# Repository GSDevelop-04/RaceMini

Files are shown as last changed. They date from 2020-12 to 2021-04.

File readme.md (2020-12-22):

<br />
<p align="center">
   <a href="https://github.com/GSDevelop-04/RaceMini">
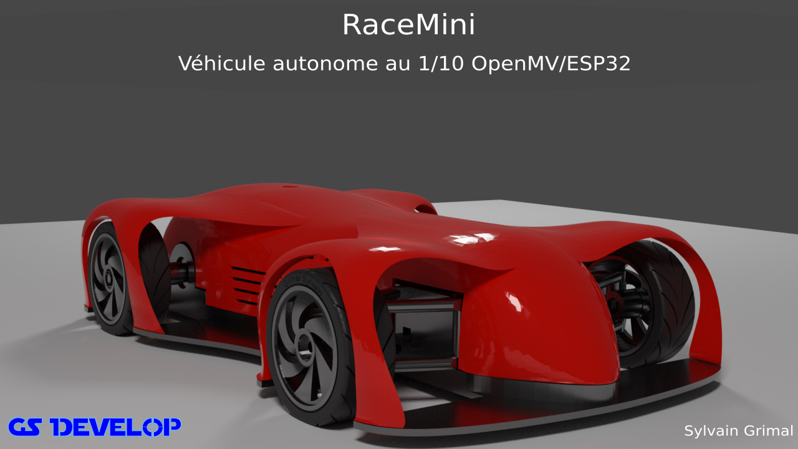
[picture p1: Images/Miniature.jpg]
    
   </a>
   <br/>
   Véhicule autonome au 1/10
   1/10 self driving car
</p>

##    1) Introduction

RaceMini est un véhicule au 1/10 d'étude sur la conduite autonome.
cliquer pour voir la vidéo sur youtube:
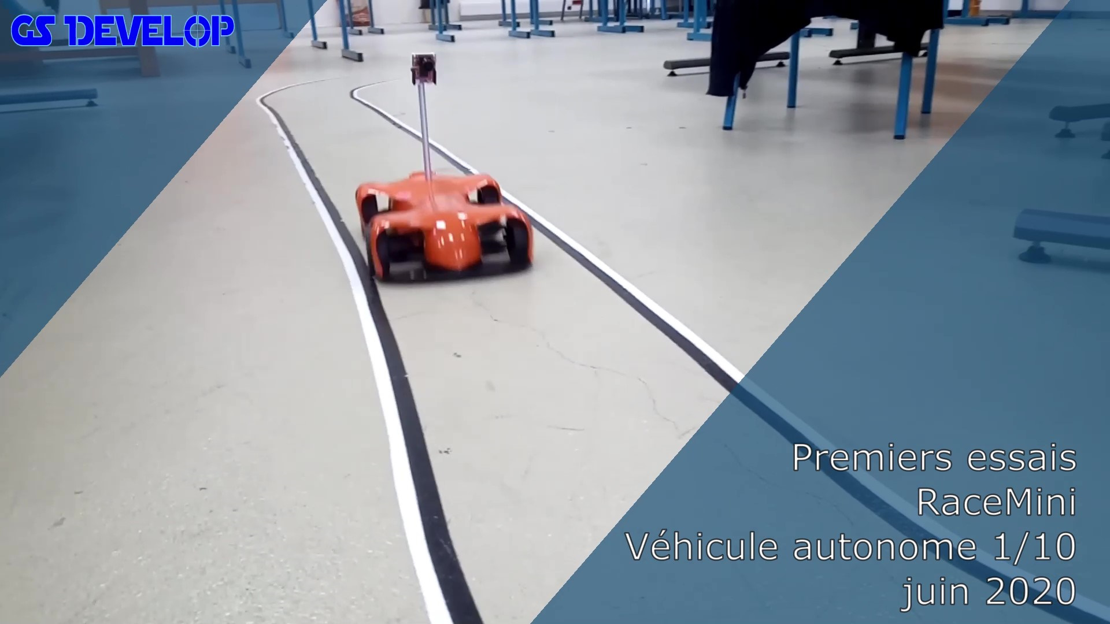
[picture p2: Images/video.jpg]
Vidéo (https://youtu.be/tJVRatMsotc)


Le véhicule peut être piloté par un smartphone via une application Android et peut fonctionner en automatique ou manuel. Il utilise la reconnaissance des marquages au sol via la transformée de Hough sur une caméra openMV M7 ou H7 

<p align="center">
 <a href="https://github.com/GSDevelop-04/RaceMini">
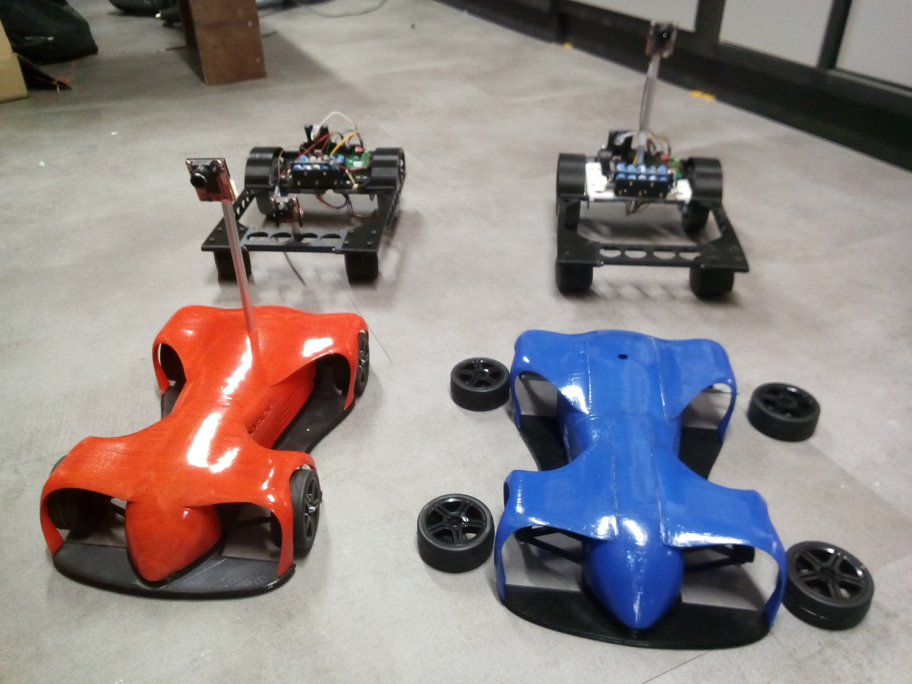
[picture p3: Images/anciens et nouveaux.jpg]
véhicules
    
 </a>
</p>

Le modèle est entierement imprimable en 3D

**Dans le dépot RaceMini vous trouverez :**

* les fichiers CAO, STL pour imprimantes 3D 20 x 20 cm ou 30 x 30 cm
* L'APK Android pour le téléphone
* Le source ESP32 pour IDE Arduino
* Le source Python pour L'OpenMV

Non obligatoire:
* Les fichiers kiCad pour la fabrication d'un circuit imprimé: il rationalise le câblage avec des connecteurs pour chaque élément du système ( carte variateur, alim 5V, camera, écran )
* Des examples de traitement de l'image (transformée de Hough et régréssion) en java script (juste pour comprendre, non utilisés dans RaceMini)

L'ensemble est sous licence **CC BY-NC-SA**

**Les éléments suivants sont nécessaires:**

* Caméra OpenMV H7 (M7 possible) **attention à l'objectif le 2,8 mm d'origine possède un champ de vision un peu limité préférer un 2 ou 2.2 mm**
* ESP32 ( Il existe de nombreux modules le CI est prévu pour un ESP32 DEVKIT V1: 30 broches)
* Carte variateur (la carte DRI0042 dispose d'une sortie 5V régulée)
* Moteur type 540 et Pignon moteur
* Un servomoteur
* batterie et interrupteur
* Visserie
* En option un écran Oled 1.3" monochrome **Attention selon le fabricant le GND et le 5V sont inversés !**

##    2) Structure matérielle.

<p align="center">
 <a href="https://github.com/GSDevelop-04/RaceMini">
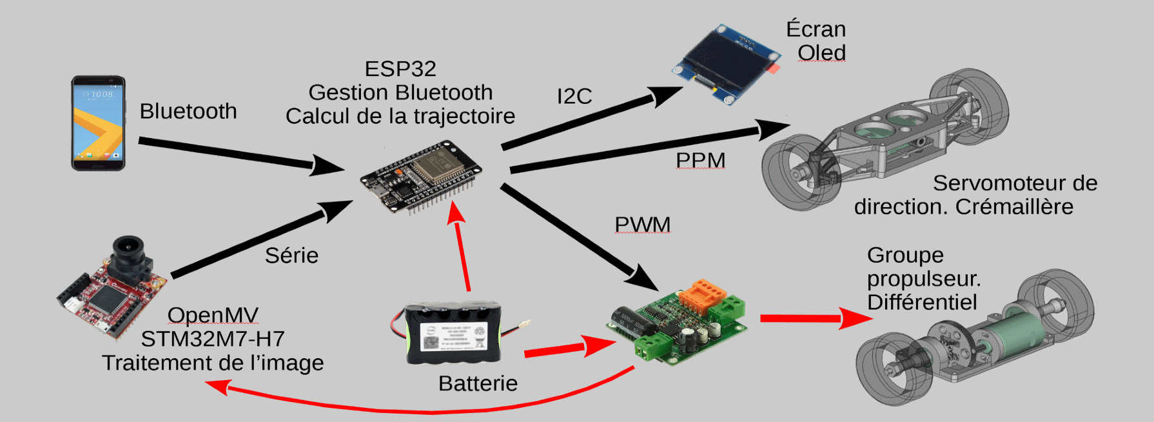
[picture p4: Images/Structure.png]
Structure
    
 </a>
</p>

la carte ESP32 reçoit les informations des marquages au sol détectés par la caméra via une liaison série et commande le moteur via une carte variateur ainsi que le servomoteur de direction.  L'application Android permet de commander le véhicule en manuel et de passer en mode automatique. En mode automatique la vitesse maximale est aussi fixée par le téléphone. 

##    2.1) Traitement de l’image

Le traitement de l’image est effectué par le microcontrôleur STM32H7 de la camera open H7. Il comprend plusieurs parties :

**Sélection des zones d’intérêt :**
Toutes les zones de l’image ne présentent pas les mêmes intérêts : un virage au loin informe qu’il faudra diminuer la vitesse avant de l’aborder (cette zone n’est pas analyser dans la version actuelle), par contre, la zone immédiatement devant votre véhicule détermine l’action sur la direction. On défini trois zones d’intérêts :
* Zone d’anticipation (bleu) *(non utilisée dans la version actuelle)*
* Zone marquage au sol droit (jaune)
* Zone marquage au sol gauche(vert)

<p align="center">
 <a href="https://github.com/GSDevelop-04/RaceMini">
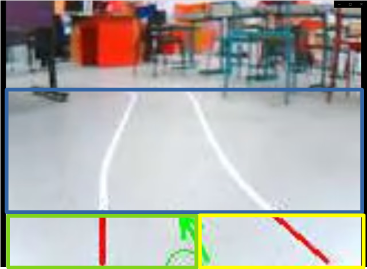
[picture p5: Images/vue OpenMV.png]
Vision
    
 </a>
</p>

Pour simplifier les zones sont rectangulaires et fixes.

* Détection des lignes dans les zones marquage au sol droit et gauche : L’algorithme utilise la transformée de Hough : chaque point sélectionné (contraste route grise et marquage blanc) sur l’écran est transformé en une sinusoïde représentant toutes les droites passant par ce point (distance de la droite par rapport à l’origine en fonction de l’angle de la droite) si plusieurs points sont alignés alors les sinusoïdes se croisent en un point image de la droite d’alignement. A l’issu de ce traitement on obtient un segment de droite pour le marquage au sol droit et un pour la gauche. Ils sont définis par les coordonnées (dans le repère de la camera) de leur extrémités.

NB : la transformée de Hough est une fonction déjà intégrée au Python de l’openMV mais un programme en javascript existe pour en comprendre le fonctionnement ( Attention les navigateurs Chrome, Firefox et le nouveau Edge -Chromium- ne supporte plus le traitement d'images sur disque, il faut charger la page html, le code javascript et l'image dans un serveur WEB)

* Calcul des segments dans le repère du véhicule à partir des coordonnées camera. Les points de la route sont supposés avoir une altitude nulle (terrain plat). Les quatre points sont ensuite transmis à l’ESP32 pour déterminer la conduite.

L’ensemble est programmé en python avec l’IDE openMV IDE.

##    2.2) Calcul de la commande de conduite.

La carte ESP32 reçoit les deux segments de droites des marquages au sol, elle détermine le CIR à partir de la médiane des deux segments (axe de la route) puis calcule la commande du servomoteur pour obtenir la bonne trajectoire :

L’ensemble est programmé dans l’IDE Arduino

<p align="center">
 <a href="https://github.com/GSDevelop-04/RaceMini">
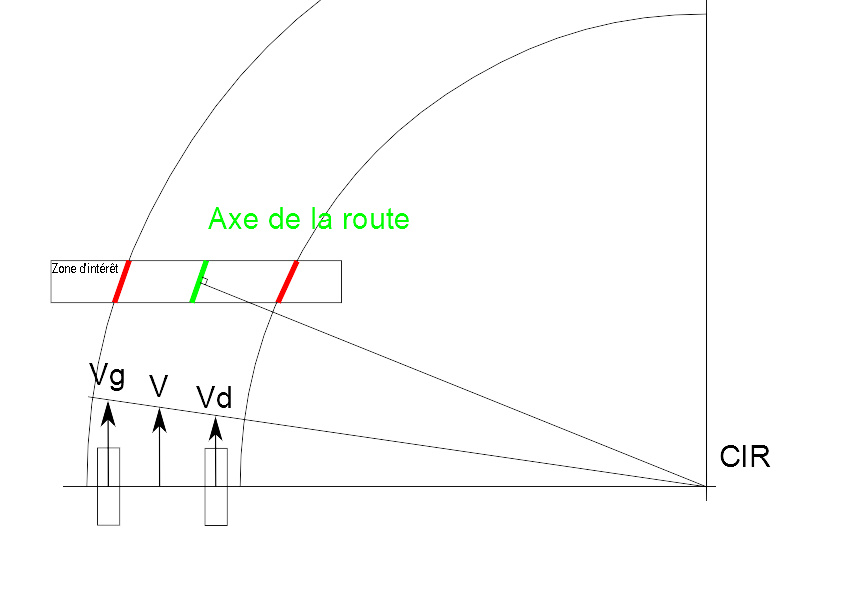
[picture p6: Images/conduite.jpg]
Schéma
    
 </a>
</p>

##    2.3) Câblage

**Liasons ESP32 Caméra:**  
* RX ESP32 (RX2) / Tx caméra (P1 uart 1 Tx)  
* TX ESP32 (TX2) / Rx caméra (P0 uart 1 RX)

**Liaisons ESP32 Variateur:**  
* ESP32 D25 / PWM 
* ESP32 D33 / IN2  // Marche avant: 1 Marche arrière: 0  
* ESP32 D32 / IN1  // Marche avant: 0 Marche arrière: 1

**Liaisons ESP32 Ecran:**  
* ESP32 D21 / OLED SDA  
* ESP32 D22 / OLED SCL
						
**Et les alimentations:** Le 5v est fourni par la carte variateur sinon utiliser un module regulateur 5V à découpage

##   3) Vidéos
* [Présentation: https://youtu.be/Jysb8A-HKZk](https://youtu.be/Jysb8A-HKZk)
* [Marquages au sol partie 1: https://youtu.be/zz7oVWdyysM](https://youtu.be/zz7oVWdyysM)
* [Marquages au sol partie 2: https://youtu.be/7tqPUZ-_XuY](https://youtu.be/7tqPUZ-_XuY)
* [Modélisation caméra sténopé: https://youtu.be/YC57ygDgGVU](https://youtu.be/YC57ygDgGVU)
* [Conduite: https://youtu.be/9OizZml_HDY](https://youtu.be/9OizZml_HDY)
* [RaceMaxi: https://youtu.be/luEXLeMDnMg](https://youtu.be/luEXLeMDnMg)

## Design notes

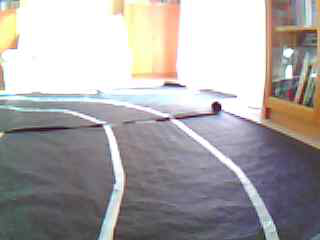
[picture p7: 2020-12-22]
Html/photo.bmp

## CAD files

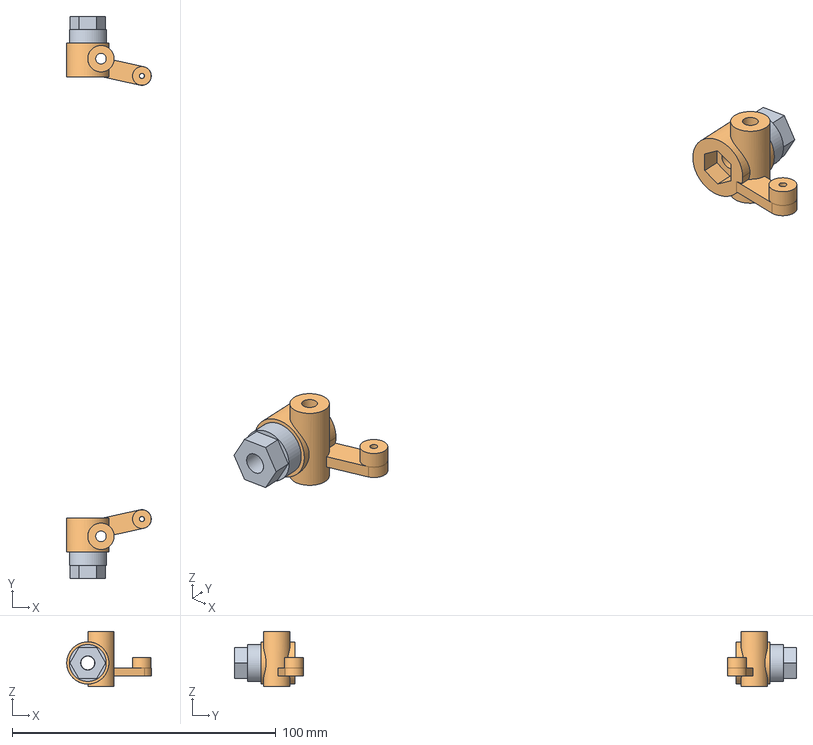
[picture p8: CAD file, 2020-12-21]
CAO/fusee.step
32.1 x 213.0 x 21.0 mm
Body046_(Mirror_#1)
Body045_(Mirror_#2)

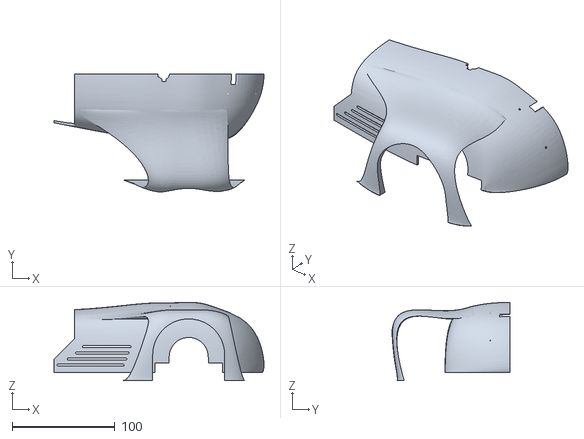
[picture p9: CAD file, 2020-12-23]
CAO/STL/Printer_20x20cm/carrosserie_arriere_gauche.stl
204.2 x 114.6 x 76.1

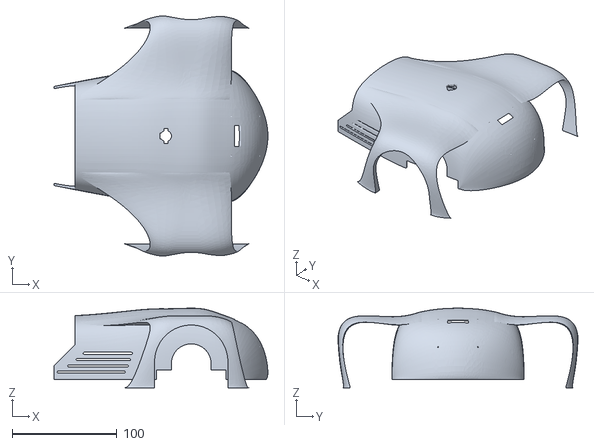
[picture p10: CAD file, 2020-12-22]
CAO/STL/Printer_30x30cm/carrosserie_arriere.stl
204.2 x 229.2 x 76.1

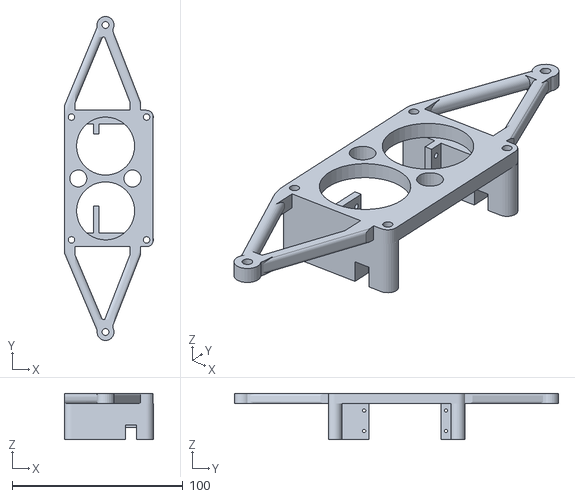
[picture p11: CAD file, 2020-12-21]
CAO/STL/suspen_avant_haut.stl
52.0 x 189.9 x 27.0

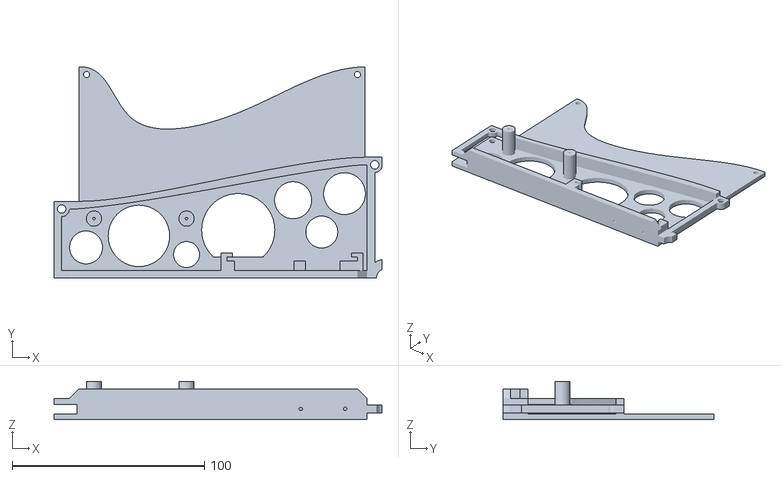
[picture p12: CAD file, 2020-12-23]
CAO/STL/Printer_20x20cm/chassis_millieu_droit.stl
170.8 x 110.0 x 20.0

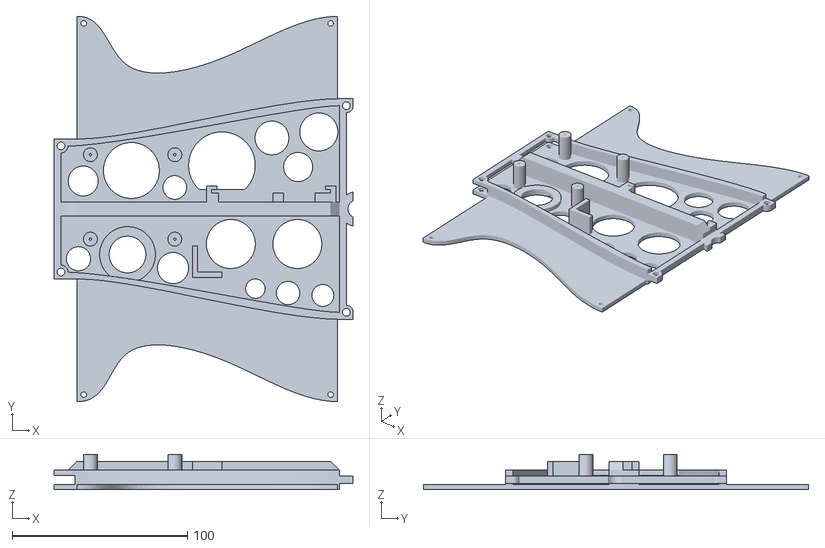
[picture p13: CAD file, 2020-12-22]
CAO/STL/Printer_30x30cm/chassis_millieu.stl
170.8 x 220.0 x 20.0

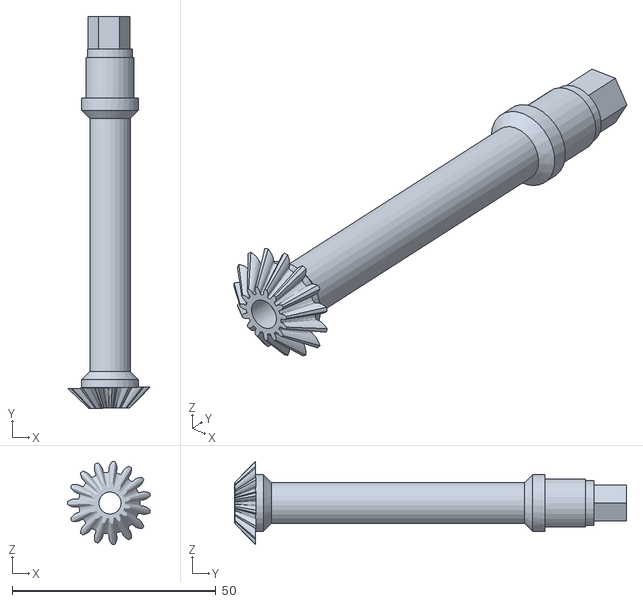
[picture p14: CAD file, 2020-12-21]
CAO/STL/transm_Droite.stl
20.3 x 96.1 x 20.4

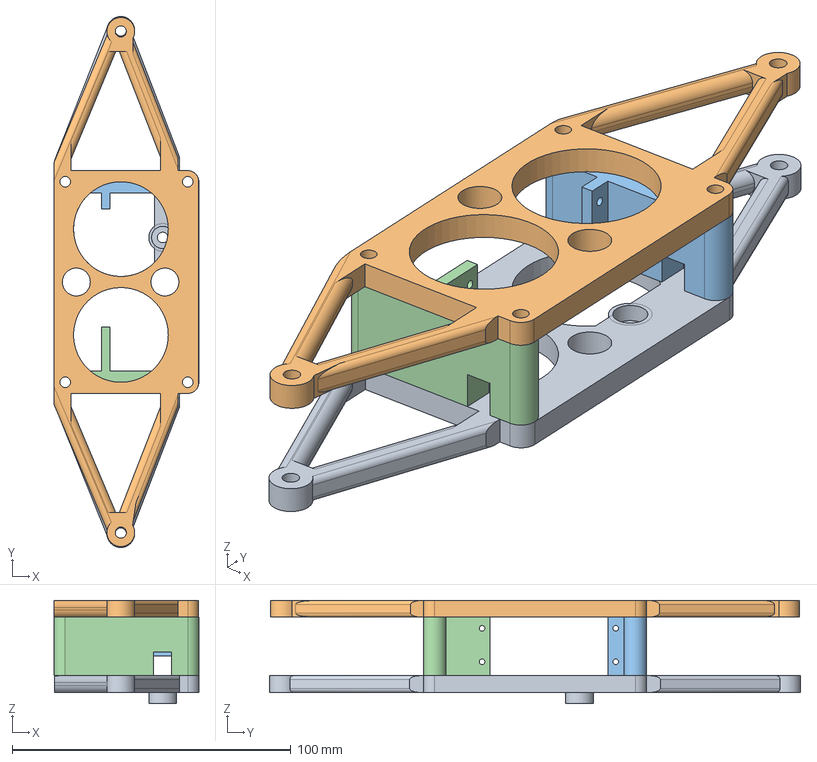
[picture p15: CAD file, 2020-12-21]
CAO/SuspAvant.step
52.0 x 190.7 x 37.0 mm
suspenAvantBas
suspenAvantHaut
supportDroit
supportGauche

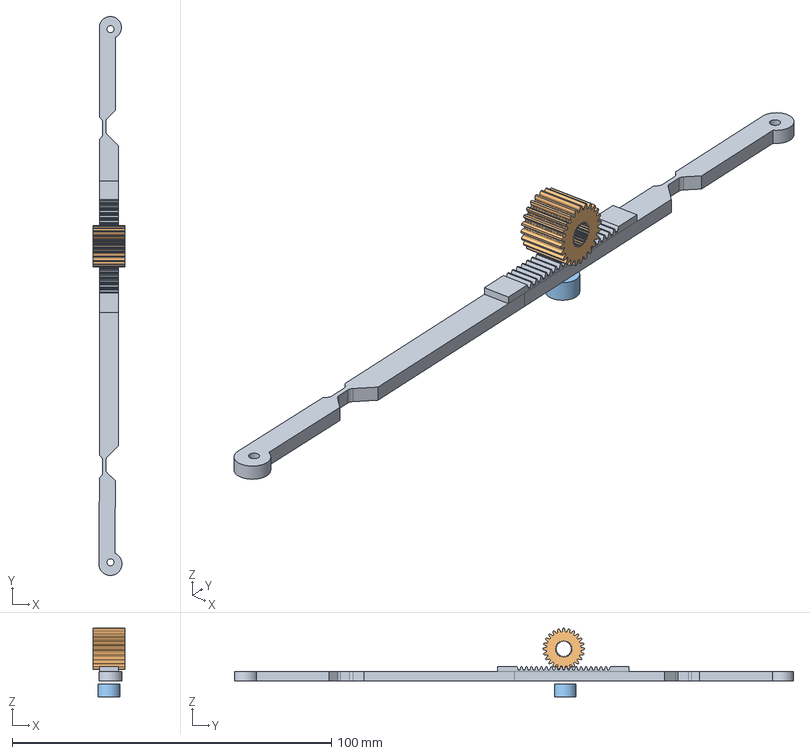
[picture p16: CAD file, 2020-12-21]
CAO/direction.step
10.0 x 175.1 x 21.5 mm
cremalliere
pignon002
poussoir

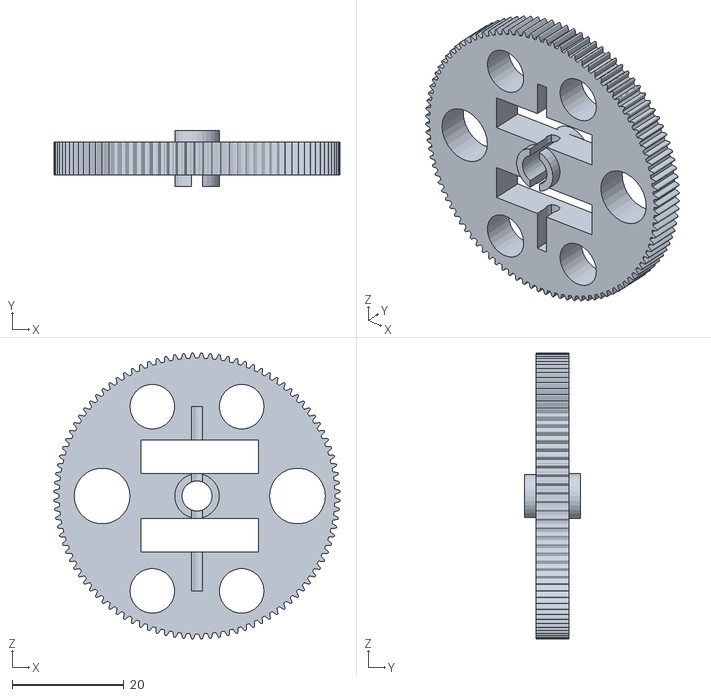
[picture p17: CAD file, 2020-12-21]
CAO/STL/couronne.stl
51.2 x 10.0 x 51.2

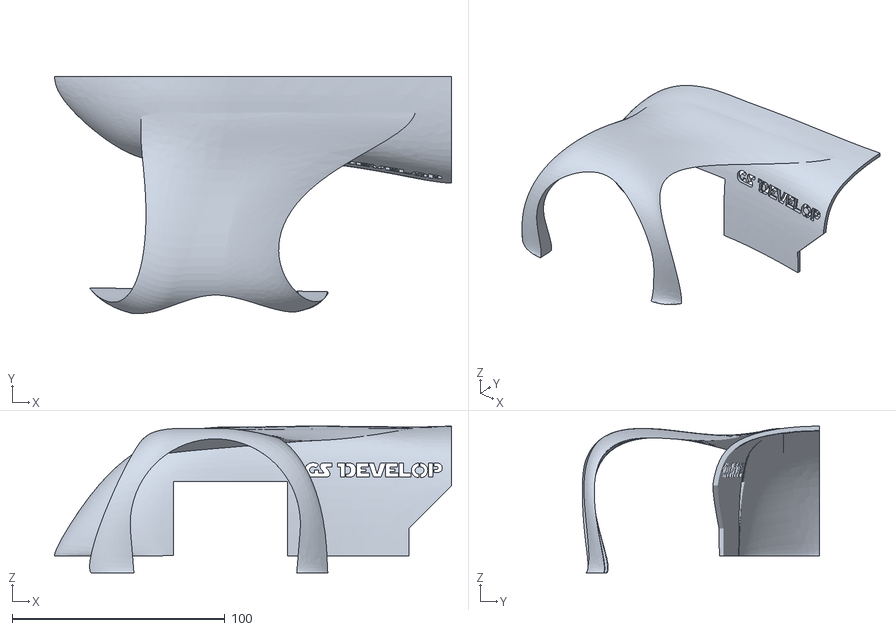
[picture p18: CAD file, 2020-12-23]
CAO/STL/Printer_20x20cm/carrosserie_avant_gauche.stl
186.6 x 111.6 x 69.1

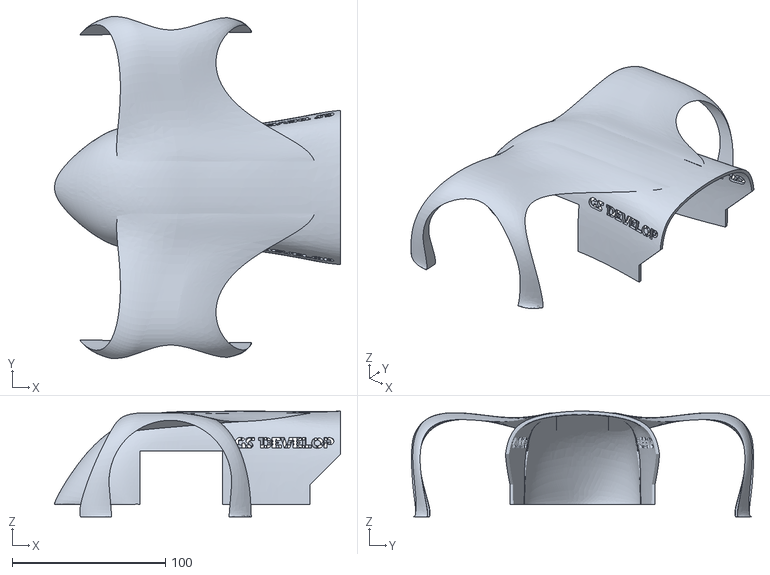
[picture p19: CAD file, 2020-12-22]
CAO/STL/Printer_30x30cm/carrosserie_avant.stl
186.6 x 223.1 x 69.1

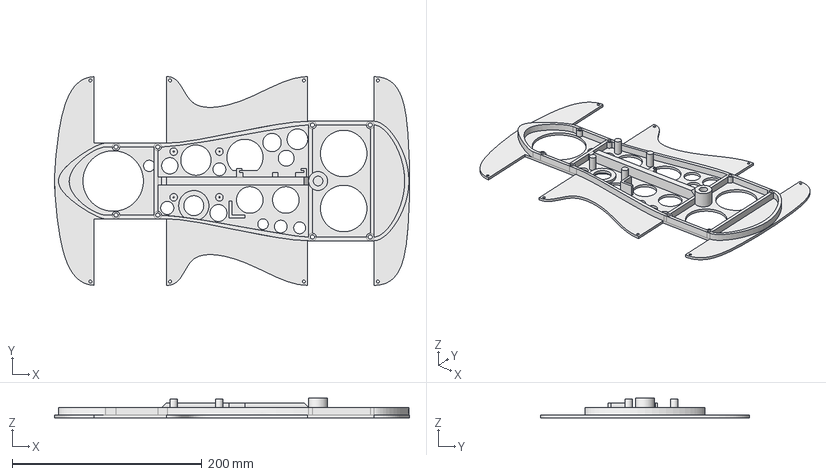
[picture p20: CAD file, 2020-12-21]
CAO/chassis.step
374.2 x 220.0 x 21.0 mm

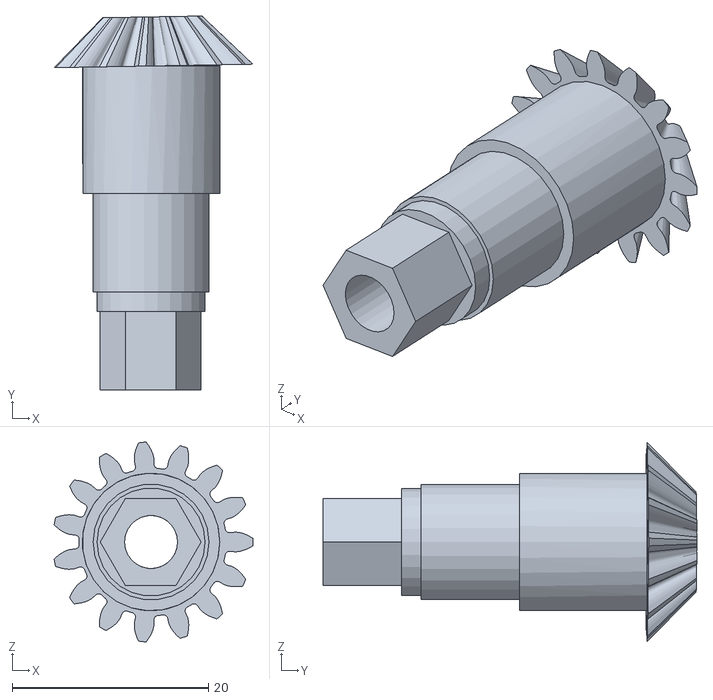
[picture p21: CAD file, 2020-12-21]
CAO/STL/transm_Gauche.stl
20.3 x 38.1 x 20.4

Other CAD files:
CAO/STL/Printer_20x20cm/carrosserie_arriere_droit.stl
CAO/pignon.FCStd
CAO/STL/pivot_Droit.stl
CAO/STL/Printer_20x20cm/chassis_millieu_gauche.stl
CAO/STL/Printer_20x20cm/carrosserie_avant_droit.stl
CAO/STL/Printer_20x20cm/chassis_arriere.stl
CAO/STL/Printer_20x20cm/chassis_avant.stl
CAO/STL/berceau.stl
CAO/STL/carrosserie.stl
CAO/STL/chassis.stl
CAO/STL/cremailliere.stl
CAO/STL/differentiel_x2.stl
CAO/STL/ecran.stl
CAO/STL/fusee_Droite.stl
CAO/STL/fusee_Gauche.stl
CAO/STL/moyeu_Arr_x2.stl
CAO/STL/moyeu_Avant_x2.stl
CAO/STL/pignon_Crem.stl
CAO/STL/pignon_Crem2.stl
CAO/STL/poussoir_Crem.stl
CAO/STL/suspen_avant_bas.stl

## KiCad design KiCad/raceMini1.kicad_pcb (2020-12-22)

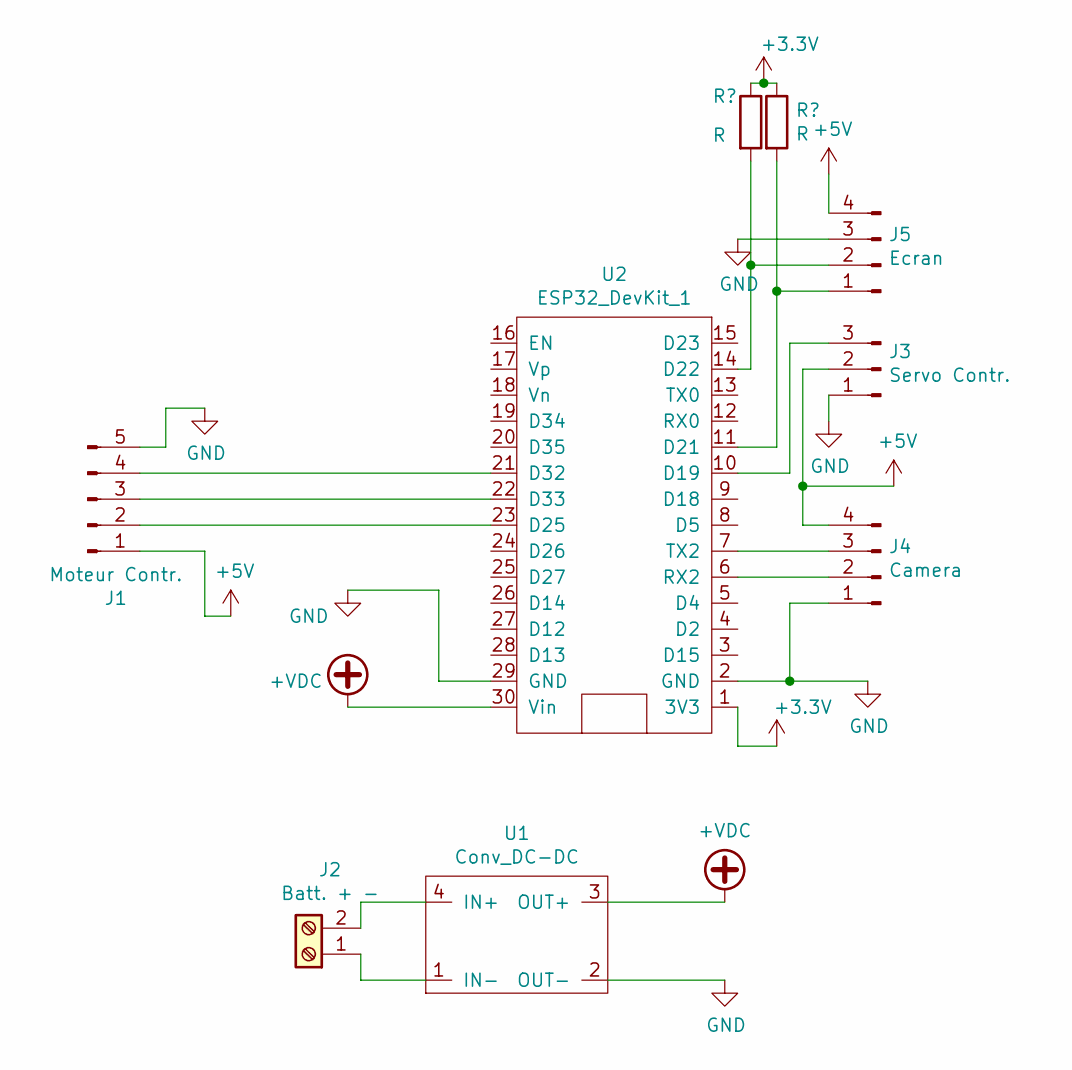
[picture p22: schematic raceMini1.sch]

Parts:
J1: Moteur Contr.; PinHeader_1x05_P2.54mm_Vertical
J2: Batt. + -; mkds_1,5-2
J3: Servo Contr.; PinHeader_1x03_P2.54mm_Vertical
J4: Camera; PinHeader_1x04_P2.54mm_Vertical
J5: Ecran; PinHeader_1x04_P2.54mm_Vertical
U1: Conv_DC-DC; Module_DC-DC_Lm2596
U2: ESP32_DevKit_1; ESP32_Devkit_DOIT_V1

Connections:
+5V: J1.1, J3.2, J4.4, J5.4
+VDC: U1.3 (OUT+), U2.30 (Vin)
GND: J1.5, J3.1, J4.1, J5.3, U1.2 (OUT-), U2.2 (GND), U2.29 (GND)
unnamed: J1.2, U2.23 (D25)
unnamed: J1.3, U2.22 (D33)
unnamed: J1.4, U2.21 (D32)
unnamed: J2.1, U1.1 (IN-)
unnamed: J2.2, U1.4 (IN+)
unnamed: J3.3, U2.10 (D19)
unnamed: J4.2, U2.6 (RX2)
unnamed: J4.3, U2.7 (TX2)
unnamed: J5.1, U2.11 (D21)
unnamed: J5.2, U2.14 (D22)

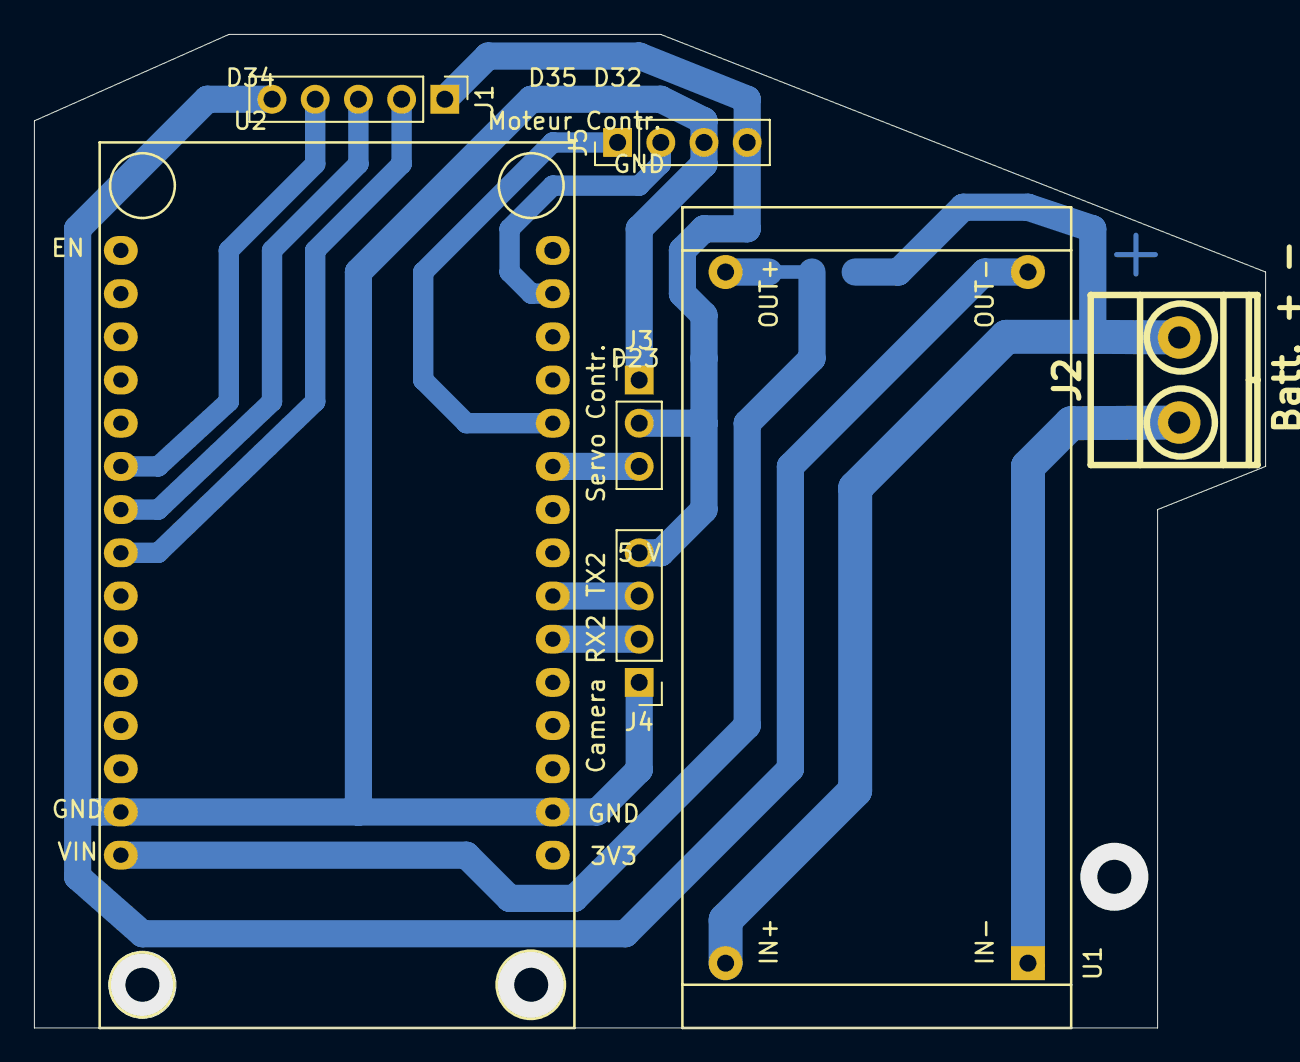
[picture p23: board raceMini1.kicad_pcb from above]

Board: 2 copper layers, 72.4 x 58.4 mm, 7 parts (0 on the bottom side), 13 nets.

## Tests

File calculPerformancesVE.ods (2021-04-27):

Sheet: Zoe
 |  |  |  |  |  |  | Zoé Renault 88 ch |  |  |  |  | 260 333 | W
 | Masse : | 1550 | kg | Couple moteur : |  | 220 | N.m | N max | 11300 | trs/min
 | Inertie : | 1705 | kg | Puissance : |  | 65000 | W | Vitesse basc : | 2821 | trs/min
 | Cx : | 0,34 |  | Rapport de réduction : 1 / |  | 9,5
0,75 | S : | 2,2 | m² | Diamètre Roues : |  | 0,6 | m |  | Vmax | 134,5
 | Crr : | 0,01
 |  |  |  | Force Motrice C0: |  | 6618 | N
incrément temps : |  | 0,25 | s |  | G0 | 0,39 | g
temps : | Force motrice C0 : | Force motrice Pmax : | Force motrice | Résistance roulement : | Résistance aérodynamique : | Résultante : | Accélération m.s-² | Vitesse : | Distance : | Km/h | trs/min
0 | 6618,3 |  | 6618,3 | 152,055 | 0,00 | 6 466,28 | 3,79 | 0,00 | 0,00 | 0,00 | 0,00
0,25 | 6618,3 |  | 6618,3 | 152,055 | 0,41 | 6 465,87 | 3,79 | 0,95 | 0,24 | 3,41 | 286,71
0,5 | 6618,3 | 65128 | 6618,3 | 152,055 | 1,65 | 6 464,63 | 3,79 | 1,90 | 0,71 | 6,83 | 573,40
0,75 | 6618,3 | 32565 | 6618,3 | 152,055 | 3,71 | 6 462,57 | 3,79 | 2,84 | 1,42 | 10,24 | 860,04
1 | 6618,3 | 21712 | 6618,3 | 152,055 | 6,59 | 6 459,69 | 3,79 | 3,79 | 2,37 | 13,65 | 1 146,59
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

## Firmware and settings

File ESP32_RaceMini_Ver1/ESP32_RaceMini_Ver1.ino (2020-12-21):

// *****************************************************************
// * Pilotage du Racemini Ver1.0001
// * Sylvain GRIMAL 2020
// * ***************************************************************

#include <HardwareSerial.h>
#include <Wire.h>
#include <U8g2lib.h>
#include "BluetoothSerial.h"
#include "config.h"

//#include <Servo.h>

#if !defined(CONFIG_BT_ENABLED) || !defined(CONFIG_BLUEDROID_ENABLED)
#error Bluetooth is not enabled! Please run `make menuconfig` to and enable it
#endif

#define ECRAN

#ifdef ECRAN
U8G2_SH1106_128X64_NONAME_F_HW_I2C u8g2(U8G2_R0, /* reset=*/ U8X8_PIN_NONE); // déclaration afficheur Oled I2C
#endif

bool freinage;

String ordreBT="";
String infoCam="";

//Servo direction;

int mode=1,n;
float dist=100,consigneVitesse=0,consigneDirection=0;

bool cam=true;

float comDirect=0, comVitesse=0;
float kp=0.5; //pas de correction de position
float pos,tangAlpha;
float xd1,yd1,xd2,yd2;
float xg1,yg1,xg2,yg2;


unsigned long tempsAff;
unsigned long tempsCom;
unsigned long tempsCli;


void setup()
{ 
  debug.begin(115200);
  
  pinMode(LED_PIN, OUTPUT);
  pinMode(IN1_PIN, OUTPUT);
  pinMode(IN2_PIN, OUTPUT);
  pinMode(PWM_PIN, OUTPUT);

 
  ledcAttachPin(PWM_PIN,PWM_CANAL); // association du PWM_CANAL à la patte PWM_PIN 
  ledcSetup(PWM_CANAL,PWM_FREQ,PWM_RES); // init du canal PWM

  //direction.attach( SERVO_PIN, SERVO_CANAL, 45, 120);
   ledcSetup(SERVO_CANAL, 50, 16); // channel, 50 Hz, 16-bit width
   ledcAttachPin(SERVO_PIN, SERVO_CANAL);   // GPIO 22 assigned to channel 1
  
  delay(1000);
  debug.println("C'est parti");  

# ifdef ECRAN
  u8g2.begin();
  delay(1000);
  debug.println("u8g2 démarré");
  affichage("Initialisation Bluetooth");
#endif  

  bluetooth.begin(NOM_BT);
  debug.println("Bluetooth activé");
  
  camera.begin(115200);
  debug.println("camera connectée");
  
  tempsAff=millis()+tempoAff;
  tempsCom=millis()+tempoCom;
  tempsCli=millis()+tempoCli;
  debug.println("Setup fini");
  
}

void loop()
{
  int8_t nb;
  float xp,yp,xv,yv;
  float alpha,deltaCrem,beta;
  
  
  // reception bluetooth
  while (bluetooth.available()>0) {
    char caract=bluetooth.read();
    //debug.print(caract);
    if (caract==13) {
      gestionCommandes(ordreBT);
      ordreBT="";
    }
    else if (caract>=32) ordreBT+=caract;
  }
  // reception camera
  while (camera.available()>0) {
    char caract=camera.read();
    //debug.print(caract);
    if (caract==13) {
      gestionCamera(infoCam);
      infoCam="";      
    }
    else if (caract>=32) infoCam+=caract;
  }


  // calcul de la commande
  if (millis()>tempsCom) {
      tempsCom=millis()+tempoCom;
      // *** Mode manuel ***
      if (mode==1) {
        comDirect=consigneDirection;
        comVitesse=consigneVitesse;
      }     
      // *** Mode auto ***
      if (mode==2) {
        xp=(xg1+xd1+xg2+xd2)/4;
        yp=(yg1+yd1+yg2+yd2)/4;
        xv=yg2+yd2-yg1-yd1;
        yv=-xg2-xd2+xg1+xd1;
        // Calcul de la commande
        #ifdef TOTAL
           alpha= atan(EMPATTEMENT*yv/(xp*yv+yp*xv-yv*DEMIVOIE));
           deltaCrem = sqrt(square(LB) -square(D-LP*cos(alpha+ALPHA0)))-LP*sin(alpha+ALPHA0)-sqrt(square(LB)-square(D-LP*cos(ALPHA0)))+LP*sin(ALPHA0);
           debug.print(deltaCrem);debug.print("\t");
           beta=deltaCrem/RP*180/PI;
           debug.println(beta);  
        #endif
        #ifdef ORDRE1
          beta=COEF1*atan(yv/xv);
        #endif
        #ifdef ORDRE2
          beta=COEF1*atan(yv/xv)+COEF2*square(atan(yv/xv));
        #endif
        
        // correction position
        comDirect=beta+kp*COEFPOS*xp/yp;
      
        
        freinage=false;
        if (square(consigneVitesse)*abs(yv/(yv*xp+yp*xv))<GMAX){
          comVitesse=consigneVitesse;
        } else {
          comVitesse=sqrt(abs(GMAX*(yv*xp+yp*xv)/yv));
          debug.println("Freinage");
          freinage=true;
        }
     }      
     commande(comVitesse,comDirect);
  }
  // Clignotement led
  if (millis()>tempsCli) {
     tempsCli=millis()+tempoCli;    
     digitalWrite(LED_PIN,!digitalRead(LED_PIN));    
  }
  // Affichage ecran
  if (millis()>tempsAff) {
     tempsAff=millis()+tempoAff;    
     if (mode==1) affichage("Manu.");
     if (mode==2) affichage("Auto.");
  }
}

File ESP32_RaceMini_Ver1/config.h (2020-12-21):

// definitions des constantes liées au materiel elec.

#define NOM_BT "RaceMini1"
#define LED_PIN 2

// Servo Direction
#define SERVO_PIN 19
#define SERVO_CANAL 2
#define COEFSERVO 18.2 // coef temps impulsion position depend du servo
#define ZEROSERVO 4915 // position 0
#define SERVOMAX 1638  // limitation rotation du servo
#define TRIM -300 

// Moteur
#define PWM_PIN 25
#define PWM_CANAL 0
#define PWM_FREQ 5000   // 5khz
#define PWM_RES 10 // 10 bits 

#define IN2_PIN 33 // 0 0 brake 1 1 libre 
#define IN1_PIN 32 // 1 0 forwward 0 1 reverse

// Tempo
#define tempoAff 200  // affichage 5 fois par seconde
#define tempoCli 500  // Clignotement led PC13 2 fois par seconde
#define tempoCom 50  //  commande 20 fois par seconde

#define debug Serial
BluetoothSerial SerialBT;
#define bluetooth SerialBT // port bluetooth déclaré en deux fois pour permettre debugage sur usb sans BT

#define camera Serial2



// Définition des constantes liées aux dimensions en cm

#define DEMIVOIE 9.0
#define EMPATTEMENT 21.8
#define LP 1.7
#define LB 3
#define D 1.4
#define RP 0.5
#define ALPHA0 14*PI/180

#define GMAX 100 // acc transversale max sinon freinage attention unité en %²/m: pourcentage de commande² pour un rayon de 1 m !

#define TOTAL // TOTAL equation complète // ORDRE1 modèle linéaire // ORDRE2 modèle quadratique
#define COEFPOS 45 // coefficent degre pour regul proportionnelle position avec kp normalise
#define COEF1 2
#define COEF2 0.2  

//#define RATIO 0.2 // ratio de vitesse si route perpendiculaire
//const float GAMMA=(1-RATIO)*4/(M_PI*M_PI); // pour relation vitesse angle

#define square(a) (a)*(a)

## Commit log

2020-12-21 premier commit
    [SuspAvant.step, berceau.stl, carrosserie.stl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]
2020-12-22 Java et KiCad
    [raceMini1.kicad_pcb, raceMini1.sch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]
2020-12-22 imprimante 30 30
    [arriere.stl, avant.stl, chassis_arriere.stl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]
2020-12-22 Maj noms
    [carrosserie_arriere.stl, carrosserie_avant.stl]
2020-12-23 imprimante 20 20
    [carrosserie_arriere_droit.stl, carrosserie_arriere_gauche.stl, carrosserie_avant_droit.stl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]
